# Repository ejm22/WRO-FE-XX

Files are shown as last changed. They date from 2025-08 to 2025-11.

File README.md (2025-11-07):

# WRO-FE-XX
Documentation for team Double-X's robot for WRO 2025 - Future Engineers.

If you're searching for the National Final version of the code, you can find the file main.py (National Final version) in the same file as run.py (International Final version). Both codes work if you'd like to try Version 1.

---

## Summary Video
This 6 minutes video summarizes our project and documentation. We recommend you watch it to easily and efficiently understand our project !

Summmary Video (https://www.youtube.com/watch?v=--gac5zhfu8 "Summary Video")

## The Team
Team Double-X is made of 2 engineering students, Michael Bruneau and Emile Jacques, and we've been teammates since 2015 !  
[Our Facebook Page since 2015](https://www.facebook.com/1WROCanadaDoubleX)

<table>
  <tr>
    <td>Michael Bruneau</td>
    <td>Emile Jacques</td>
  </tr>
  <tr>
    <td>Michael Bruneau</td>
    <td>Michael Bruneau</td>
  </tr>
</table>

---

## The Robot (Slef)
Have you ever had methods in your class needing the 'self' input to access the object ? If so, we are absolutely sure you've at least misstyped it once. Which is what we did throughout the entire project. With the amount of times Emile typed 'Slef', we had to give this name to our robot haha.

### Pictures

<table>
  <tr>
    <td align="center"><strong>GIF</strong><br></td>
  </tr>
</table>

---

<table>
  <tr>
    <td align="center"><strong>Top</strong><br></td>
    <td align="center"><strong>Front</strong><br></td>
    <td align="center"><strong>Left</strong><br></td>
  </tr>
  <tr>
    <td align="center"><strong>Bottom</strong><br></td>
    <td align="center"><strong>Back</strong><br></td>
    <td align="center"><strong>Right</strong><br></td>
  </tr>
</table>

#### Recent Modifications
A few hardware modifications were brought since these pictures were taken. 
- **Stepper Motor & Driver Wiring:** The wiring was simplified to remove one terminal block and multiple solid wires.
- **White Tape Replaced:** The white tape that used to be on top of the servo motor was replaced by a thin 3D-printed white plate.
- **Canadian Flags:** A few Canadian flags were added to personalized our robot, since we are proud to represent Canada once again !

---

## Performance Videos
### Challenge 1
[Open Challenge Video for International Final on Youtube: ](https://youtu.be/sGerwb-1xKw)

[Open Challenge Video for National Final on Youtube: ](https://youtu.be/OgR29EYXkdw)

### Challenge 2
[Obstacle Challenge Video for International Final on Youtube: ](https://youtu.be/1s1PPFf92Jc)

[Obstacle Challenge Video for National Final on Youtube: ](https://youtu.be/s9inOFHvLYA)

---

## Mobility Management

- **Dimensions:** width 135mm, length 285mm for tight turns and component fit, height 248mm.  
  [Why we chose those dimensions](mech/README_mech.md#14-dimensions-choice)
- **Drive Motor:** NEMA 17 stepper (precise, no encoder needed).
We calculated the needed torque for our application, and considering a rolling resistance and an 85% gearbox efficiency, the NEMA-17's torque is greater than the needed torque. Here's how we calculated it : 


  [More Information on Drive Motor Choice](elec/README_elec.md#13-motor-choice)
- **Steering Motor:** Standard servo motor for simple, precise steering.  
  [More Information on Steering Motor Choice](elec/README_elec.md#14-direction-control--servo-motor)
- **3D-Printed Structure:** Three-layer design (base, middle, top) for easy assembly and access.  










  [More Pictures & Info Here](mech/README_mech.md#3-final-3d-printed-structure)
- **Custom Mounts:** Holders for servo, stepper, switches, camera, and stepper coupler.  
  [Pictures Here](mech/README_mech.md#4-mounting-and-coupling)
- **Steering:** Initially parallel beams, now Ackermann geometry, 3D-printed after Lego prototyping. 




  [Steering CADs](mech/README_mech.md#12-steering-system)
- **Wheels:** Spike Prime wheels (56mm diameter, 14mm thick) for compactness and grip.  
  [Why We Chose Spike Prime Wheels](mech/README_mech.md#11-wheel-choice)
- **Differential:** Compact differential for rear wheels, made of Lego pieces individually bought on BrickLink.  
  [Why We Chose This Differential](mech/README_mech.md#13-differential-rear-wheels)

- **Iterations:** As you can see in the following image, this was an iterative project with many versions of each part. 


#### Here's a general view of the robot in SolidWorks. The second picture is an exploded view of it, so you can see the detachable pieces.
<table>
  <tr>
    <td>Michael Bruneau</td>
    <td>Emile Jacques</td>
  </tr>
</table>

### Controlling the Motors
This following document explains the C++ code used by the Arduino to control both the stepper and servo motors.  
[Motor Control](code/md/motor_control.md)

---

## Building Instructions
- **Parts list**\
Make sure you have all components ready before starting: 3D-printed parts, motors, drivers, electronics, screws, and connectors. A complete detailed table with quantities, sources, and usage is included below for reference.\
[Click here to open the parts list](XX_Parts_Lists.pdf)
- **3D Printing Parts**\
Using any 3D printer, start by 3D printing the necessary parts for the assembly. We used a Prusa Core 1. Every part needed has a STL file which you can use with any printer. If you're adventurous and want to modify a part, open the STEP file in your favorite CAD software. If you're unsure of what part you're printing, make sure to open the PNG file which contains a picture of the part.\
[Click here to open this folder](mech/CAD_3D_Printed_Pieces)
- **Adjust the Driver**\
The DRV8825 has a tiny screw to adjust the maximum current output. This isn't a big problem since the NEMA 17 stepper motor requires barely a few hundred mA, but it's good practice to set a limit. Use the DRV8825 Adjuster we custom-built to set this limit ! You can recreate this adjuster using the following drawing.\
[DRV8825 Adjuster Drawing](elec/Driver_Calibration_Circuit.pdf)
<table>
  <tr>
    <td>Michael Bruneau</td>
    <td>Emile Jacques</td>
  </tr>
</table>

- **Assemble the Robot**\
Mechanically assembling the robot is quite straight-forward. The tricky part comes with the electrical connections. Make sure you follow correctly the following electrical drawings.\
*Take notes, the drawings are quite small ! Make sure to download the PDF files to be able to zoom.*\
[Electrical Drawings](elec/Electric_Planning.pdf)

---

## Power & Sense Management

### Hardware Architecture
The "brain" of our robot is a Raspberry Pi 5, coded in Python. Connected to it is the Pi Camera 3 wide angle, meaning that all data will be directly given to the Pi. The Pi is also connected to an Arduino Uno R3, coded in C++, which controls the servo motor and the stepper motor's driver. The Arduino receives its commands via serial communication from the Pi. The stepper motor's driver will then power the motor if needed. 

<table>
  <tr>
    <td>Michael Bruneau</td>
  </tr>
</table>

- **Controller:** Raspberry Pi 5 (vision+logic, master) + Arduino Uno R3 (motor driver, slave).  
  [Why We Chose the Pi 5](elec/README_elec.md#21-main-components-choice)
- **Stepper Driver:** DRV8825 on breadboard (micro-stepping).  
  [Why We Chose the DRV8825](elec/README_elec.md#21-main-components-choice)
- **Camera:** Pi Camera 3 Wide for large FOV—helps with vision and parking.  
  [Why We Chose the Pi Camera 3 Wide](elec/README_elec.md#21-main-components-choice)
- **Wiring:** Terminal blocks and breadboard help organize and distribute power/signals.  
  [More details](elec/README_elec.md#3-wiring-and-distribution)
- **Power:** 4s1p 18650 Li-ion (14.4V) pack, DC/DC converter to 5V, terminal blocks for safe distribution.  

### Battery Runtime Calculation (1 hour at max load)
Here is the table of component power requirements : 

| Component | Voltage Requirement | Current Requirement |
|---|:---:|:---:|
| **Raspberry Pi 5** | 5V | up to 3A |
| **Arduino Uno R3** | 5V | ~40mA |
| **NEMA 17 Stepper Motor**  | 12V (via driver) | Via Driver (so 0)  |
| **DRV8825 Stepper Driver** | 12V | ~700mA |
| **Servo Motor (steering)** | 5V | ~700mA |
| **Pi Camera 3 Wide** | 5V (via Pi) | Via Pi (so 0) |
| **DC/DC Converter** | 14.4V in, 5V out | 80% efficiency |
| **4s1p 18650 Li-Ion Pack** | 14.4V | up to 2.85A |

Given the table, here's a quick calculation for **1 hour** of operation at maximum power:

#### Step 1: 5V Side Consumption
- Raspberry Pi 5: 3.00A  
- Arduino Uno R3: 0.04A  
- Servo Motor: 0.70A  
- **Total 5V current:** 3.74A  

**Power at 5V:**  
3.74A × 5V = **18.7W**

#### Step 2: Account for DC/DC Efficiency (80%)
**Battery power needed for 5V rail:**  
18.7W / 0.8 = **23.4W**

#### Step 3: Add Stepper Driver (12V side)
DRV8825: 0.70A × 12V = **8.4W**

#### Step 4: Total Battery Power & Current
**Total power from battery:**  
23.4W (5V rail) + 8.4W (stepper) = **31.8W**  
**Current from battery:**  
31.8W / 12V = **2.65A**

#### Step 5: Battery Capacity Needed (1 hour)
2.65A × 1h = **2.65Ah**

#### Conclusion
At full load, 1 hour of runtime requires **2.65Ah** at 12V.  
The 4s1p 18650 pack (2.85Ah) is just enough for 1 hour at max draw.

**In practice:** Most components use less than max (the Pi uses less than half), the robot is often idle, the DC/DC's efficiency is actually closer to 86%, and the stepper driver is disabled at 0 speed. In real use, the robot lasts 3–4 times longer, so the 4s1p pack is more than sufficient. We also have 8 cells in total so while 4 of them are used, the other 4 are charging, and it takes less time to charge batteries to full than to empty them.

### Security Measures
We added many security mesures on our robot to assure a safe robot and minimal reliability issues with parts.
- **Fuse:** We use a 3A fuse between the battery pack and the rest of the robot's electrical connexions to ensure the pack's safety.
- **Switches:** A Main Switch and a Driver Switch are installed. We are then able to shutdown the stepper motor in one click, or the entire robot in one different click.
- **Front Wing (Bumper):** A front wing was added to the front of the robot to make it crashproof. This keeps the important mechanical and electrical parts of the robot from absorbing the shock.
- **Terminal Blocks:** Terminal blocks were added for safer and easier electrical connexions. No short circuits in sight :)
- **Battery Pack Orientation:** Some of the cells would sometimes move too much from an impact between the robot and the wall, even with the bumper. By rotating the pack by 90 degrees, the cells won't be able to move.
- **Voltmeter:** A voltmeter was added on the side of the robot, connected right after the fuse, to show the battery pack's voltage. This is extremely useful since we preferably never want our voltage to go below 10.8V (for cell preservation). 

---

## Obstacle Management

### Vision Methods and Decision Making

This part of the readme explains how the computer vision pipeline drives steering decisions for the robot. It explains the following:
- Wall following (how far up the image it sees black on both sides)
- Obstacle handling
- Inner/outer crash detection
- Arbitration (how actions are chosen)

### 1) Image pipeline (inputs used by algorithms)

The camera pipeline produces these images used by the algorithms:
- polygon_image: binary map of the drivable corridor (walls are black=0, free space is white=255)
- display_image: BGR frame used for debug overlays (text, lines, circles)
- obstacle_image / pink_obstacle_image: binary masks for color obstacles
- blueline_image & orangeline_image: per-color masks for lap tracking

<table>
  <tr>
    <td align="center">
      <strong>Display Image Open Challenge</strong><br>
      
    </td>
  </tr>
  <tr>
    <td align="center">
      <strong>Display Image Obstacle Challenge</strong><br>
      
    </td>
  </tr>
  <p>*The display image contains new information such as the state of the program, a timer and the speed.</p>
  <tr>
    <td align="center">
      <strong>Polygon Image</strong><br>
      
    </td>
  </tr>
  <tr>
    <td align="center">
      <strong>Obstacle Image</strong><br>
      
    </td>
  </tr>
  <tr>
    <td align="center">
      <strong>Lines Image</strong><br>
      
    </td>
  </tr>
</table>

See [`CameraManager`](code/XX_2025_package/classes/camera_manager.py) and [`ImageTransformUtils`](code/XX_2025_package/utils/image_transform_utils.py).

### 2) Wall following calculations

Goal: steer so that the nearest wall is observed at a desired “depth” (how far up the image) and “lateral” position (how far from the side).

How it works:
- The robot scans for black (wall) pixels:
  - Bottom-up along a small band of columns near the followed side (“how far up” the wall appears).
  - Side-in from the image center toward the followed side along a small band of rows (“how far inward” the wall appears).
- These samples are averaged into (avg_x, avg_y) by [`ImageAlgorithms.find_wall_to_follow`](code/XX_2025_package/classes/image_algoriths.py).
- [`ImageAlgorithms.calculate_servo_angle_from_walls`](code/XX_2025_package/classes/image_algoriths.py) builds a PD-like controller:
  - Proportional term: error = (avg_x + avg_y) − threshold.
  - Derivative term: change of that error across frames.
  - Direction sign (LEFT/RIGHT) is taken from context to steer the correct side.
- Gains and the target threshold come from [`CHALLENGE_CONFIG`](code/XX_2025_package/classes/image_algoriths.py) via [`ImageAlgorithms.calculate_wall_threshold_kp_kd`](code/XX_2025_package/classes/image_algoriths.py), adapting behavior per challenge/lap.
- Corner detection: a large negative jump in the wall error derivative marks a “corner,” returned via the is_corner flag for higher-level logic.

Notes:
- “How far up it sees black on both sides” is embodied in the dual scans (bottom-up and side-in) that together capture corridor geometry.

### 3) Obstacle handling calculations

When an obstacle is present (green/red/pink block), the robot computes an avoidance “object line,” converts it to an angle, and arbitrates with wall following. The robot will accelerate between obstacles.

Process in [`ImageAlgorithms.find_obstacle_angle_and_draw_lines`](code/XX_2025_package/classes/image_algoriths.py):
- Safety first: [`ImageAlgorithms.check_outer_wall_crash`](code/XX_2025_package/classes/image_algoriths.py) and [`ImageAlgorithms.check_inner_wall_crash`](code/XX_2025_package/classes/image_algoriths.py). If a frontal collision risk is detected, immediately force a sharp evasive turn.
- Find the largest / lowest obstacle rectangle on the color mask image and classify its color using HSV.
- Draw a guidance line from the obstacle center to a safe floor target x:
  - Green → pass on the right; Red → pass on the left (policy).
- Convert that line’s geometry into an object angle, then map it to a servo angle with a color-specific offset in [`ImageAlgorithms.calculate_servo_angle_from_obstacle`](code/XX_2025_package/classes/image_algoriths.py).
- Inner safety: [`ImageAlgorithms.check_inner_wall_crash`](code/XX_2025_package/classes/image_algoriths.py) disables obstacle passing if the inner wall is too close (falls back to wall following).

What the “mapping” does:
- It shifts and scales the object angle around straight-ahead so the servo turns just enough to skirt the obstacle, clamped to safe servo limits.

### 4) Crash detection

Two safety checks override normal behavior:
- Outer wall crash: [`ImageAlgorithms.check_outer_wall_crash`](code/XX_2025_package/classes/image_algoriths.py) probes a fixed point ahead, and if it’s black in the polygon image, commands an emergency turn away from the outer wall.
- Inner wall crash: [`ImageAlgorithms.check_inner_wall_crash`](code/XX_2025_package/classes/image_algoriths.py) probes several points near the inner side; if too close (especially with a short obstacle), obstacle passing is suppressed.

### 5) Arbitration: choosing the action

Both proposals are produced:
- Wall-following angle from [`ImageAlgorithms.calculate_servo_angle_from_walls`](code/XX_2025_package/classes/image_algoriths.py)
- Obstacle angle from [`ImageAlgorithms.calculate_servo_angle_from_obstacle`](code/XX_2025_package/classes/image_algoriths.py) (or None if no obstacle)

Selection rule in [`ImageAlgorithms.choose_output_angle`](code/XX_2025_package/classes/image_algoriths.py):
- If there is a valid obstacle-avoidance angle, prefer it; otherwise, follow the wall.

Priority in practice:
1) Outer wall crash → emergency avoidance
2) Valid obstacle avoidance → use it
3) Inner wall too close while avoiding → fall back to wall following
4) Otherwise → wall following

### 6) Tuning notes

- Controller gains/thresholds are challenge-aware via [`CHALLENGE_CONFIG`](code/XX_2025_package/classes/image_algoriths.py) and refined per lap in [`ImageAlgorithms.calculate_wall_threshold_kp_kd`](code/XX_2025_package/classes/image_algoriths.py).
- The direction (LEFT/RIGHT) simply flips the sign of the control so one algorithm works for both sides.
- Corner detection from the wall controller’s derivative is used elsewhere (for example during parking) to trigger special maneuvers.

───────────────

### Block diagrams:
<table>
  <tr>
    <td align="center">
      <strong>Open Challenge Block Diagram</strong><br>
      
    </td>
  </tr>
  <tr>
    <td align="center">
      <strong>Obstacle Challenge Block Diagram</strong><br>
      
    </td>
  </tr>
  <tr>
    <td align="center">
      <strong>Obstacle Challenge Action Decisions</strong><br>
      
    </td>
  </tr>
</table>

### Extras
- Lap tracking and direction detection [details here.](code/md/laps_and_direction.md)
- Parking [details here.](code/md/parking.md)

---

## Software Key Components

- **Communication:** Serial communication via USB cable between Arduino and Pi (using custom protocol).\
  [Communications Protocol Details](code/md/communication.md)
- **Raspberry Pi Environment Setup:** Downloading utilities on your Pi, creating a virtual environment (venv), and installing dependencies.\
  [How to Setup your Raspberry Pi](code/md/raspberry_pi_setup.md)

---

## Possible Improvements
- **Holding the Raspberry Pi Better:**
The Raspberry Pi is currently fixed with black electric tape. Ideally, a simple detachable 3D-printed part could hold it.
- **Cutting Power Automatically at 10.8V:**
Whenever the battery pack voltage is below 10.8V, we would open the circuit to ensure that the circuit shuts down.
- **Replacing the Breadboard with Custom PCB:**
Instead of using a breadboard with mediocre cable management, we would simply add a custom PCB where we would solder the necessary cables in place.
- **Adding Lateral Distance Sensors:**
The current one-camera solution is complex to work with for the parallel parking. We would add distance sensors on both sides to detect the parking parking when we pass by, and to improve the overall wall detections across both challenges.
- **Adding Dynamic Ranges for Colors:**
The HSV ranges we have are set for the entire run. If we had more time, we would love to add dynamic ranges to account for walls / obstacles that appear lighter because of lighting on certain part of the wall, because of windows for example.

---

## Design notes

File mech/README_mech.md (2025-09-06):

### Mechanical Design Approach
[All PNG, STP and STL files are in this directory](./CAD_3D_Printed_Pieces/)
#### 1\. Basic Mechanical Choices

###### **1.1 Wheel Choice**
We chose Spike Prime wheels (56mm diameter, 14mm thickness) for their compactness, grip on vinyl, and familiarity. Larger wheels would make the robot harder to control and take too much space; smaller wheels would complicate the design and lower ground clearance.


###### **1.2 Steering System** 
- **Prototype:** Parallel beam Lego steering (two beams linked at ends) was tested. It suffered from drifting during turns due to both wheels turning at the same radius.

- **Ackermann Steering:** Lego-based Ackermann system was built to solve drifting. Final version is 3D-printed to fit the custom base plate.


###### **1.3 Differential (Rear Wheels)** 
A differential built out of Lego pieces individually bought on BrickLink allows the rear wheels to turn at different speeds for smooth cornering. Printing our own gears would have a low value/complexity ratio, so we built it with Lego pieces. It is very compact and works perfectly fine.
###### **1.4 Dimensions Choice**
We linked both the direction and differential wheel systems together. Considering all the components we would need to fit (Pi, Arduino, stepper motor, ...), we decided to keep a minimum approximate 50mm margin for the width, so max 150mm. A robot that has a big length/width ratio has a big turning radius (like a Formula 1 car). After testing different sizes, we decided to make the robot about 285mm long and 135mm wide. This makes the turning radius small enough to leave barely any room while turning around a pillar. 

---

#### 2\. Structural Prototypes

- **Lego Prototype:** Used 15-hole beams, L-beams, and frames to connect steering and differential systems.
- **Motor Positioning:** Stepper motor centrally located, axle connected to differential.
- **Wheel Space:** Front kept thin for steering range.
- **First Layer:** Held drive motor, DC/DC converter, and servo.


---

#### 3\. Final 3D-Printed Structure

- **Base Plate:** Holds wheel systems, stepper, DC/DC, and servo.
<table>
  <tr>
    <td align="center">
      <strong>BasePlaqueV4 CAD</strong><br>
      
    </td>
  </tr>
  <tr>
    <td align="center">
      <strong>BasePlaqueV4 Installation</strong><br>
      
    </td>
  </tr>
</table>

___

- **Middle Plate:** Holds battery pack, Arduino, terminal blocks, stepper driver (on breadboard), and switches.
<table>
  <tr>
    <td align="center">
      <strong>MiddlePlaqueV4 CAD</strong><br>
      
    </td>
  </tr>
  <tr>
    <td align="center">
      <strong>MiddlePlaqueV4 Installation</strong><br>
      
    </td>
  </tr>
</table>

___

- **Top Plate:** Holds Raspberry Pi 5, Pi Camera, and driver terminal block.

<table>
  <tr>
    <td align="center">
      <strong>TopPlaqueV4 CAD</strong><br>
      
    </td>
  </tr>
</table>

___

- **3D Views of Complete Product**

<table>
  <tr>
    <td align="center">
      <strong>Left Side View</strong><br>
      
    </td>
  </tr>
  <tr>
    <td align="center">
      <strong>Top View</strong><br>
      
    </td>
  </tr>
  <tr>
    <td align="center">
      <strong>Bottom View</strong><br>
      
    </td>
  </tr>
</table>

---

#### 4\. Mounting and Coupling

- Custom holders for servo, stepper, switches, and camera.


___

- Stepper coupler connects motor to the differential.


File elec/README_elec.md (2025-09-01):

### Electrical Design Approach

#### 1\. Motorization

###### **1.1 Motor Option 1 : DC Motor**
DC motors are simple to control (on/off), useful for continuous forward movement, but require an encoder to determine position for precise tasks.
###### **1.2 Motor Option 2 : Stepper Motor**
Stepper motors move in discrete steps by activating electromagnets sequentially. They are ideal for short, precise movements and allow accurate position control without an encoder.
###### **1.3 Motor Choice**
We chose the stepper motor because it eliminates the need for an encoder, offers very precise position control (especially for parking), and is a new challenge to explore. The only complexity added is in task scheduling in software, which is manageable.
We also already had a NEMA 17 stepper motor, light and low consuming, which perfectly fitted on the base.
###### **1.4 Direction Control : Servo Motor**
A servo motor was selected for steering because it does not require a separate driver, has only three wires, and provides precise control.

---

#### 2\. Electric/Electronic Architecture

###### **2.1 Main Components Choice**
- **Processing:**  
  The robot uses a Raspberry Pi 5 as the master computer, handling camera input and all high-level decision logic. The Pi needs 5V at up to 3A.
- **Motor Control:**  
  An Arduino Uno R3 acts as the slave controller, receiving commands from the Pi and driving the motors. The Arduino requires 5V at 40mA (negligible).
- **Power:**  
  The stepper driver needs 12V. We use a 4s1p pack of 3.6V 18650 Li-Ion cells (14.4V, 2.85A). 14.4V is distributed via terminal blocks, then stepped down to 5V with a DC/DC converter for the Pi and Arduino.
- **Stepper Driver:**  
  The DRV8825 was chosen for its small size and micro-stepping ability (necessary for precise stepper control). Placed on a breadboard for easy connections.
- **Camera:**
  The Pi Camera 3 Wide module was chosen over the Pi Camera 3 module to have a wider field of view (FOV), necessary for more precision when parking, and helpful throughout the rest of the challenge as well.

---

#### 3. Wiring and Distribution
- **Terminal blocks** provide safe, compact power distribution for 14.4V and 5V rails.
- **Breadboard** is used for convenient connection of the stepper driver,  toggle switches, servo motor and other small electrical connections.

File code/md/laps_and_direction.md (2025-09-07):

# Direction Determination (Challenge 1 and 2) and Lap Tracking

This section explains:
- How the robot picks its driving direction at the start of Challenge 1 and Challenge 2
- How laps are tracked using a simple, debounced state machine

## Challenge 1: Direction from Blue vs Orange Line Length

At the start of Challenge 1, the robot decides whether to follow the left or right wall by comparing the detected lengths of the blue and orange lines. The decision is made in [`ImageAlgorithms.get_direction_from_lines`](code/XX_2025_package/classes/image_algoriths.py):
- If the blue line is longer than the orange line → follow LEFT
- Otherwise → follow RIGHT

Internally it reads per-frame measurements prepared by the camera pipeline (for example: `camera_manager.length_blue` and `camera_manager.length_orange`) and sets the direction in context.

Example (simplified):

```python
# Decide direction using line lengths (Challenge 1)
def get_direction_from_lines(self):
    # length_blue / length_orange are computed in the camera pipeline
    direction = Direction.LEFT if self.camera_manager.length_blue > self.camera_manager.length_orange else Direction.RIGHT
    self.context_manager.set_direction(direction)
```

Where it’s called in the main flow:
- See Challenge 1 setup in [code/XX_2025_package/main.py](code/XX_2025_package/main.py).

## Challenge 2: Direction from Free-Space (Left vs Right Half)

In Challenge 2, the robot decides the initial direction by comparing how much free space (white pixels) exists on the left half vs the right half of the drivable mask (`polygon_image`). This logic is in [`ImageAlgorithms.get_direction_from_parking`](code/XX_2025_package/classes/image_algoriths.py):
- Count white pixels in left half and right half of the binary polygon image
- If left has more white → LEFT, else → RIGHT

Example (simplified):

```python
# Decide direction from how open each half is (Challenge 2)
def get_direction_from_parking(self, camera_object):
    left_white = np.sum(camera_object.polygon_image[:, :ImageTransformUtils.PIC_WIDTH // 2] == 255)
    right_white = np.sum(camera_object.polygon_image[:, ImageTransformUtils.PIC_WIDTH // 2:] == 255)
    direction = Direction.LEFT if left_white > right_white else Direction.RIGHT
    self.context_manager.set_direction(direction)
```

Where it’s called in the main flow:
- See Challenge 2 setup in [code/XX_2025_package/main.py](code/XX_2025_package/main.py).

## Lap Tracking: Windowed Color Detection + State Machine

Laps are tracked by watching a small window near the center-bottom of the frame and advancing a state machine when the expected color appears. The sequence depends on the driving direction:
- Direction LEFT: expect BLUE then ORANGE
- Direction RIGHT: expect ORANGE then BLUE
- After detecting the pair, wait (debounce) before looking for the next pair

Window used for detection in [`LapTracker.process_image`](code/XX_2025_package/classes/lap_tracker.py):
- Rows: PIC_HEIGHT − 130 to PIC_HEIGHT − 30
- Columns: ±20 pixels around the center x

State machine (LEFT direction) in [`LapTracker._process_left_direction`](code/XX_2025_package/classes/lap_tracker.py):
- INITIAL_STATE → LOOKING_FOR_BLUE
- LOOKING_FOR_BLUE: if BLUE seen → LOOKING_FOR_ORANGE
- LOOKING_FOR_ORANGE: if ORANGE seen → increment quarter, go to WAITING_STATE
- WAITING_STATE: after ~0.5s debounce → LOOKING_FOR_BLUE

```python
def _process_left_direction(self, detected_color):
    # INITIAL → LOOKING_FOR_BLUE
    # WAITING → after 0.5s → LOOKING_FOR_BLUE
    # LOOKING_FOR_BLUE + BLUE → LOOKING_FOR_ORANGE
    # LOOKING_FOR_ORANGE + ORANGE → increment quarter → WAITING
    if self._state == LapState.INITIAL_STATE:
        self._state = LapState.LOOKING_FOR_BLUE

    if self._state == LapState.WAITING_STATE:
        if self.time_stamp == 0:
            self.time_stamp = time.time()
        if time.time() - self.time_stamp >= 0.5:
            self._state = LapState.LOOKING_FOR_BLUE
            self.time_stamp = time.time()

    elif self._state == LapState.LOOKING_FOR_BLUE and detected_color == Color.BLUE:
        self._state = LapState.LOOKING_FOR_ORANGE

    elif self._state == LapState.LOOKING_FOR_ORANGE and detected_color == Color.ORANGE:
        self.context_manager.increment_quarter_lap_count()
        self._state = LapState.WAITING_STATE
```

State machine (RIGHT direction) in [`LapTracker._process_right_direction`](code/XX_2025_package/classes/lap_tracker.py) mirrors the logic:
- INITIAL_STATE → LOOKING_FOR_ORANGE
- LOOKING_FOR_ORANGE: if ORANGE seen → LOOKING_FOR_BLUE
- LOOKING_FOR_BLUE: if BLUE seen → increment quarter, go to WAITING_STATE
- WAITING_STATE: after ~0.5s → LOOKING_FOR_ORANGE

Quarter and lap accounting:
- Every time the color pair completes, [`ContextManager.increment_quarter_lap_count`](code/XX_2025_package/classes/context_manager.py) is called.
- The context tracks quarter count and laps; when enough quarters have been seen, the lap count increases.
- [`ContextManager.is_last_quarter`](code/XX_2025_package/classes/context_manager.py) and [`ContextManager.has_completed_laps`](code/XX_2025_package/classes/context_manager.py) are used to slow down or stop after the goal.

Block diagram:
<td>lap_drawio</td>
<br><br>

## End-to-End Usage Snippet

In the main loop ([code/XX_2025_package/main.py](code/XX_2025_package/main.py)):

```python
# Challenge 1: direction from lines
image_algorithms.get_direction_from_lines()

# Challenge 2: direction from free-space split
image_algorithms.get_direction_from_parking(camera_manager)

# While driving: update lap tracking from the window
lap_tracker.process_image(camera_manager.cnt_blueline, camera_manager.cnt_orangeline)

# Example of reacting to final quarter
if context_manager.is_last_quarter():
    speed = 4000  # slow down on final approach
```

This approach gives a robust start-direction choice for both challenges and a simple, debounced lap tracker.

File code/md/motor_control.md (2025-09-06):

# How We Control the Motors

This document explains how the drive and steering motors of Team Double-X's robot are controlled using Arduino, focusing on our actual implementation and challenges.

---

## 1. Overview

Our robot uses:
- **NEMA 17 Stepper Motor** for driving the rear wheels (precise position & speed control).
- **Servo Motor** for steering the front wheels (Ackermann geometry).

The motors are controlled by an **Arduino Uno R3** that receives high-level commands from a Raspberry Pi 5 and drives the motors using dedicated libraries and electronic drivers.

---

## 2. Hardware Architecture

- **Stepper Motor Driver:** DRV8825, chosen for its microstepping ability and compact design.
- **Connections:**  
  - Stepper motor uses STEP, DIR, and ENABLE pins.
  - Servo motor uses a single PWM pin (ANGLE_PIN).
- **Power:**  
  - Stepper driver powered by 12V from a Li-Ion pack.
  - Arduino and Pi powered via a DC/DC converter.

---

## 3. Arduino Software Implementation

Our code for motor control is written in C++ and runs on the Arduino. The logic is split between stepper (drive) and servo (steering) control.

### Stepper Motor Control (Drive)

A stepper motor functions by receiving pulses which activate and deactivate magnets, turning the motor. When decelerating, a stepper can't keep its precision if it stops receiving steps, hence why we need to gradually lower the speed. We use the FlexyStepper library, because it can manage those decelerations. The command logic is our own. The driver is **enabled** only when movement is required; otherwise, it is disabled to prevent overheating.

```cpp
#include <FlexyStepper.h>

const int DIR_PIN = 10;
const int STEP_PIN = 9;
const int ENABLE_PIN = 2;

FlexyStepper stepper;

void setup() {
    stepper.connectToPins(STEP_PIN, DIR_PIN);
    pinMode(ENABLE_PIN, OUTPUT);
    digitalWrite(ENABLE_PIN, LOW); // Enable driver by default
}

void loop() {
    // Example: Move the robot if a command is received
    if (shouldMove()) {
        digitalWrite(ENABLE_PIN, LOW); // Enable driver
        stepper.setSpeedInStepsPerSecond(commandedSpeed);
        stepper.setAccelerationInStepsPerSecondPerSecond(2000);
        stepper.moveRelativeInSteps(commandedSteps);
    } else if (currentSpeedIsLowEnough()) {
        digitalWrite(ENABLE_PIN, HIGH); // Disable driver to avoid overheating
    }
}
```

### Servo Motor Control (Steering)

Steering is achieved with a standard Servo library. The servo receives new angles as commands are processed.

```cpp
#include <Servo.h>
const int ANGLE_PIN = 11;

Servo steeringServo;

void setup() {
    steeringServo.attach(ANGLE_PIN);
}

void loop() {
    int steeringAngle = getSteeringAngle();
    steeringServo.write(steeringAngle); // Angle: 36-136
}
```
*Note: The angle at which the servo is straight is 86 degrees. The maximum angles for our Ackermann steering are 36 and 136 degrees.*

---

## 4. Control Flow

1. **Command Reception:**  
   The Pi sends commands to the Arduino (distance, speed, steering angle).
2. **Motion Execution:**  
   - Arduino sets the stepper speed, servo angle, and target position.
   - Driver ENABLE is managed based on demand and speed.
3. **Safety & Scheduling:**  
   - The driver is disabled when no motion is needed, or the speed is near zero, to prevent overheating.
   - Motion complete functions ensure safe synchronization.

---

## 5. Temperature Analysis

A major issue we encountered is **driver overheating**. The DRV8825 gets extremely hot even with moderate use, especially if it's left enabled while idle. To address this, our code disables the driver whenever:
- The demanded speed is zero and the actual speed is low enough.
- No commands are received for a while.

Below are thermal images showing the results of our code:

<table>
  <tr>
    <td align="center">
      <strong>Stepper Driver and Servo Motor Temperatures</strong><br>
      
    </td>
  </tr>
  <tr>
    <td align="center">
      <strong>Robot Temperature Overview</strong><br>
      
    </td>
  </tr>
</table>

*Images show that the driver temperature is around 40 degrees Celsius, which is very normal. We do not have pictures, but it would previously be so hot that touching the driver could cause serious burns*

---

## 6. References

- [FlexyStepper Library Documentation](https://github.com/Stan-Reifel/FlexyStepper)
- [DRV8825 Datasheet](https://www.ti.com/lit/ds/symlink/drv8825.pdf?HQS=dis-dk-null-digikeymode-dsf-pf-null-wwe&ts=1752710261679)
- [Driver Circuit Used on our Robot: How to Adjust Current Limit](https://www.makerguides.com/drv8825-stepper-motor-driver-arduino-tutorial/)
- *Main Arduino code: [`code/arduino/src/main.cpp`](../code/arduino/src/main.cpp)*

---

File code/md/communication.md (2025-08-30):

# Communication Protocol

## Pi-Arduino Communication

The Raspberry Pi and Arduino communicate via USB serial connection. The Pi sends formatted commands to control the robot's movement, while the Arduino sends status updates back to the Pi.

### Communication Setup
- **Connection**: USB serial between Raspberry Pi and Arduino
- **Baud Rate**: 115200
- **Protocol**: Text-based commands with specific delimiters

### Command Format

#### Pi → Arduino (Movement Commands)
Commands for movement follow the format: `m{angle},{speed}.`
If there is a target distance: `t{angle},{speed},{target}`

| Command Format | Description | Example |
|---|---|---|
| `m{angle},{speed}.` | Move command with steering angle and motor speed | `m90,5500.` |
| `t{angle},{speed},{target}.` | Move command with angle, motor speed and target | `t90,5500,3000` |
| `10000000!` | Set target command (10000000 means never stop moving) | `10000000!` |

**Parameters:**
- `angle`: Servo angle for steering (typically 30-150, where 90 is straight)
- `speed`: Motor speed value (0-6000+ range)
- `target`: Motor rotation target in steps (0.1559 mm per 1 step) 
- `.` : Move command terminator
- `!` : New target command terminator

#### Arduino → Pi (Status Updates)
| Message | Description |
|---|---|
| `1` | Challenge 1 button pressed |
| `2` | Challenge 2 button pressed |
| `0` | Stop button pressed |
| `F` | Target reached after target movement command |

### Code Implementation

**Arduino Side** (`main.cpp`):
- Sends button press notifications to Pi
- Listens for serial commands
- Parses movement commands to extract angle and speed
- Controls servo and stepper motor accordingly
- Sends stop movement command after target reached

**Pi Side** (`main.py`):
- Listens for button press status from Arduino
- Handles challenge selection and stop commands
- Sends movement commands based on computer vision analysis

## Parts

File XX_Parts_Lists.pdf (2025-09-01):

Autonomous driving car Parts List WRO FE 2025
Team Double-X, Canada
Revision 2025-09-01
Item | P/N | Description | MFR | Source | Qty | Usage | Total Cost
1 | INR-18650-P30B | 3.7V 18650 cell | Molicel | 18650BatteryStore.com | 4 | Power pack | 28
2 | a15062200ux0651 | DPDT toggle switch | Uxcell | Amazon.ca | 2 | Power switches | 16
3 | 114090052 | Battery holder 18650 4 cells | Seeed Technology Co Digikey | 1 | Battery holder | 2
4 | 39367pb02 | Wheel 56 X 14 | Lego Group | Bricklink.com | 4 | Mechanical structure | 16
5 | KLF014 | Fuse holder | Kolacen | Digikey | 1 | Power | 1
6 | DC001 | 12V Male+Female 2.1x5.5MM DC Power Jack Plug Adapter Daykit | Amazon.ca | 1 | Power plugs | 2
7 | Generic | Radial Electrolytic Capacitor, 100uF, 16V | Generic | Amazon.ca | 1 | Stepper driver circuit | 0.5
8 | CER-795 | CERRXIAN 90 Degree USB A to B Cable | Lemeng | Amazon.ca | 1 | Pi to Arduino cable | 6.5
9 | SJ-15 | DRV8825 Stepper Motor Driver | SazkJere | Amazon.ca | 1 | Stepper driver | 5
10 | CA-EL-CP-006 | Mini Breadboard | Elegoo | Amazon.ca | 1 | Stepper driver circuit | 2
11 | X00413AO5J | Maixbomr Right Angle USB C to 2 Pin Bare Wire | Maixbomr | Amazon.ca | 1 | Pi power cable | 6
12 | 39100-1910 | Terminal blocks clear, 12 pos, 8 mm pitch | Molex | Mouser | 2 | Power connections | 5
13 | HS-225BB | Cored Nylon Gear 24T Analog Mini Servo | Hitec | Robotshop | 1 | Direction motor | 30
14 | RB-Ard-34 | Arduino Uno R3 USB Microcontroller | Arduino | Robotshop | 1 | Microcontroller | 28
15 | PI5-8GB-STR128-C4-BLK | Raspberry Pi 5 Starter Kit - Turbine Black | Raspberry Pi | Canakit | 1 | Main computer | 225
16 | PYBE30-Q24-S5-DIN | DC-DC converter 12V - 5V 6amps 30W | CUI | Digikey | 1 | Generate 5V from battery | 57
17 | B099JXQN6K | Polymaker PLA Filament 1.75 mm | Polymaker | Amazon.ca | 1 | Mechanical structure | 32
18 | BasePlaqueV4 | 3D printed base plate | Double-X | 3D printed | 1 | Mechanical structure | 0
19 | MiddlePlaqueV4 | 3D printed middle plate | Double-X | 3D printed | 1 | Mechanical structure | 0
20 | TopPlaqueV4 | 3D printed top plate | Double-X | 3D printed | 1 | Mechanical structure | 0
21 | CouplingV3 | 3D printed coupler | Double-X | 3D printed | 1 | Mechanical structure | 0
22 | ServoHolderV2 | 3D printed servo holder | Double-X | 3D printed | 1 | Mechanical structure | 0
23 | StepMotorBracket | 3D printed stepper holder | Double-X | 3D printed | 1 | Mechanical structure | 0
24 | FrontWingV2 | 3D printed bumper | Double-X | 3D printed | 1 | Mechanical structure | 0
25 | CamHolderV4 | 3D printed camera holder | Double-X | 3D printed | 1 | Mechanical structure | 0
26 | DirectionRods3 | 3D printed direction rod long | Double-X | 3D printed | 1 | Mechanical structure | 0
27 | DirectionRodsShort3 | 3D printed direction rod short | Double-X | 3D printed | 1 | Mechanical structure | 0
28 | DirectionTabs | 3D printed direction tabs (LH and RH) | Double-X | 3D printed | 1 | Mechanical structure | 0
29 | ButtonHolder | 3D printed switch holder | Double-X | 3D printed | 1 | Mechanical structure | 0
30 | 17HS4023 | Stepper motor NEMA 17 | Pancake Motor | Abra electronics | 1 | Drive motor | 27
31 | 527-1 | Raspberry Pi Camera module 3 wide + cable | Raspberry | Pishop | 1 | Camera | 49
32 | 3737 | Axle 10L | Lego Group | Bricklink.com | 2 | Rear axles | 0.5
33 | 87083 | Axle 4L with stop | Lego Group | Bricklink.com | 2 | Front axles | 0.5
34 | 3705 | Axle 4L | Lego Group | Bricklink.com | 1 | Stepper main axle | 0.25
35 | 3713 | Bushing | Lego Group | Bricklink.com | 8 | Mechanical structure | 0.5
36 | 4265 | half bushing | Lego Group | Bricklink.com | 4 | Mechanical structure | 0.25
37 | 6589 | Bevel gear 12 tooth | Lego Group | Bricklink.com | 3 | Mechanical structure | 0.25

38 | 62821b | Gear differential 28 tooth bevel | Lego Group | Bricklink.com | 1 | Mechanical structure | 1
39 | 64179 | Frame | Lego Group | Bricklink.com | 1 | Mechanical structure | 0.5
40 | JF-0039 | SPDT toggle switch | Jianfeng Store | Amazon.ca | 1 | Selector switch | 2
41 | PBS-110-XR | SPST push button momentary | Twidec | Amazon.ca | 1 | Start button | 1.7
42 | LS-1280 | M3 socket head screws, multiple length | HPGJLEE | Amazon.ca | 33 | Mechanical structure | 0.5
| | | | | | Total | 545.95

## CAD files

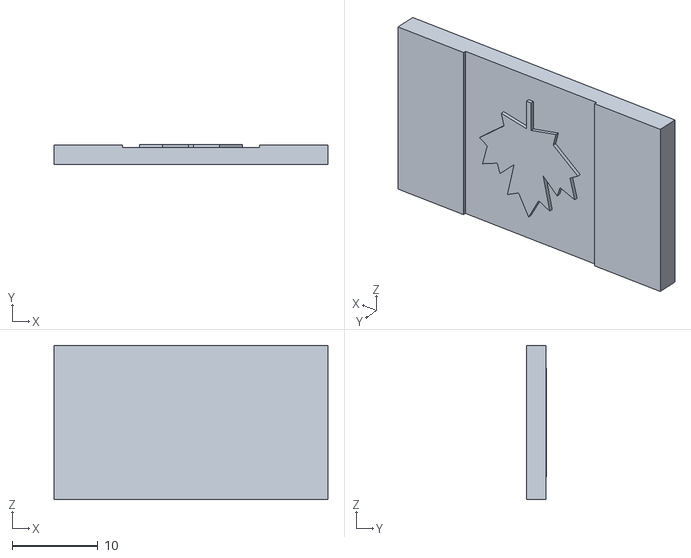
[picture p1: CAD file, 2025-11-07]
mech/CAD_3D_Printed_Pieces/CanadianFlag.STL
32.0 x 2.38 x 18.0

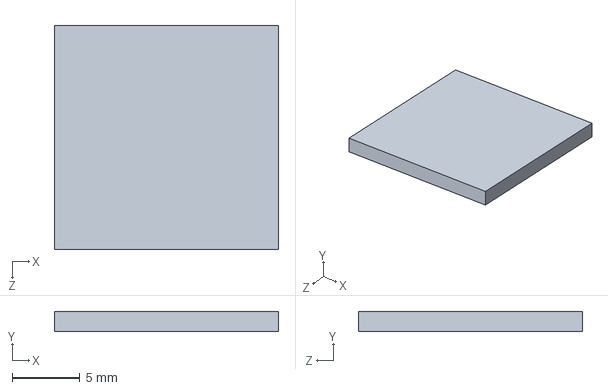
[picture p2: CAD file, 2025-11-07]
mech/CAD_3D_Printed_Pieces/ServoCover.SLDPRT
16.5 x 1.50 x 16.5 mm

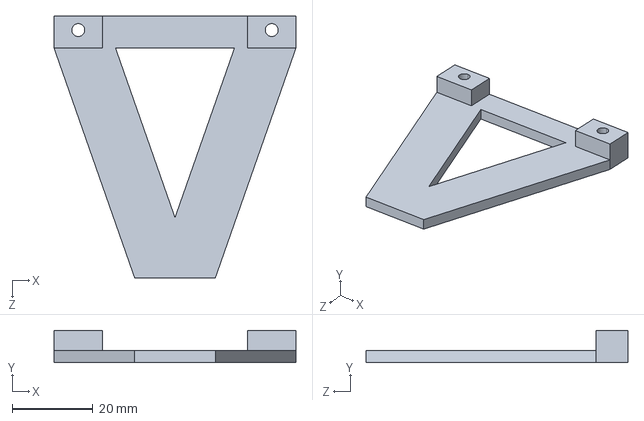
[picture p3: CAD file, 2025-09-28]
mech/CAD_3D_Printed_Pieces/FrontWingV2.STEP
60.0 x 8.00 x 65.0 mm

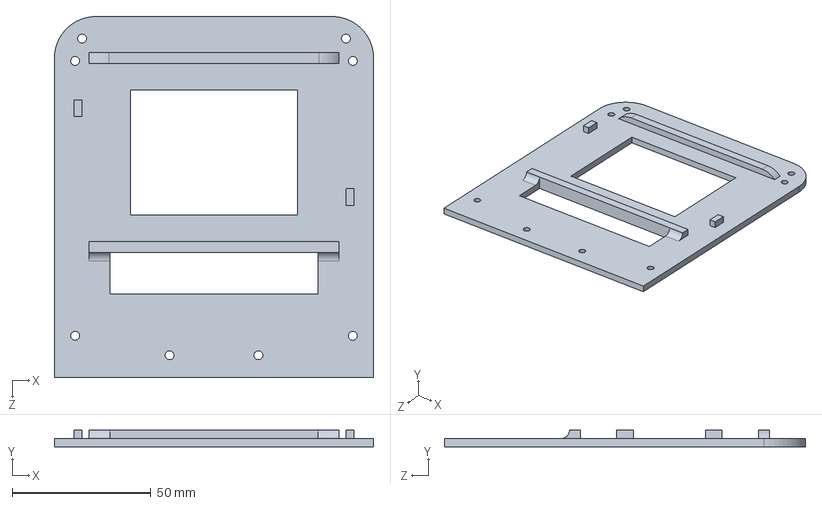
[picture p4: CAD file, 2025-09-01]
mech/CAD_3D_Printed_Pieces/TopPlaqueV4.STEP
115.0 x 6.00 x 130.0 mm

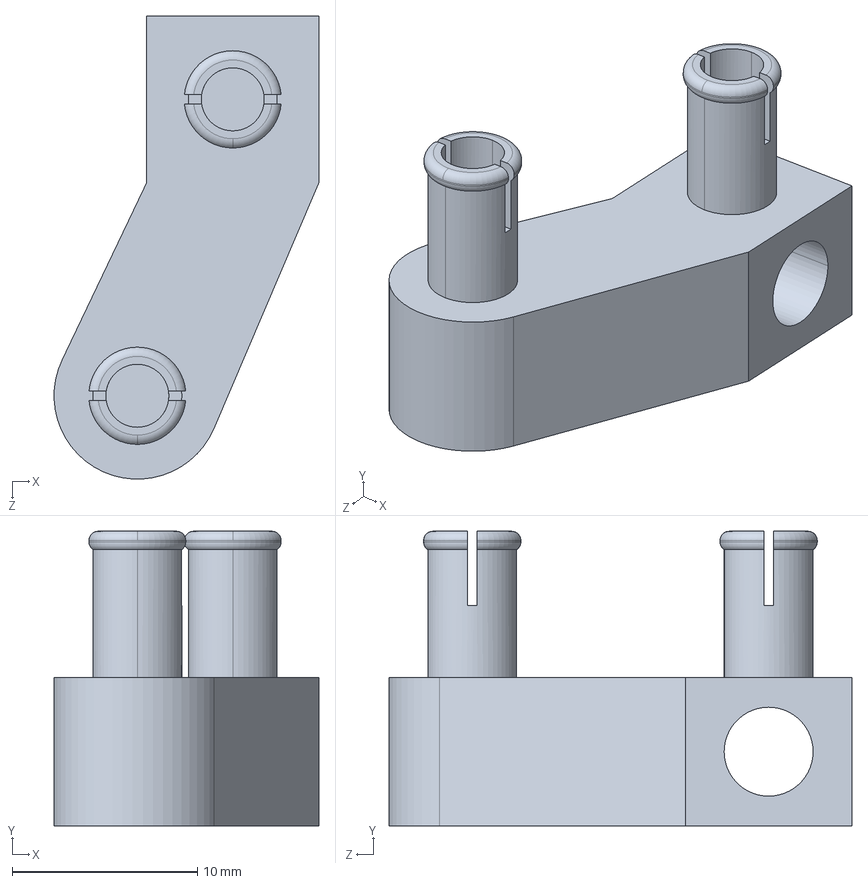
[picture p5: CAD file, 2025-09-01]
mech/CAD_3D_Printed_Pieces/DirectionTabsRH.STEP
14.3 x 15.9 x 25.0 mm

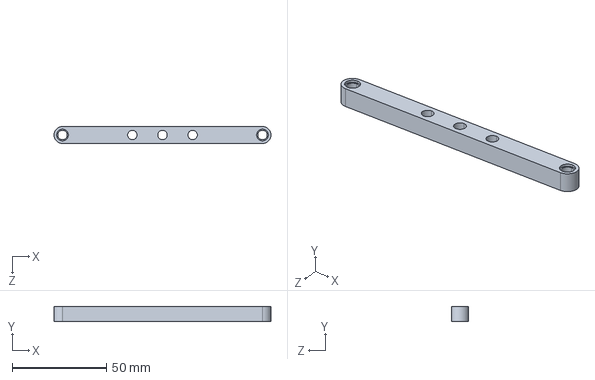
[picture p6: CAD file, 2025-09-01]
mech/CAD_3D_Printed_Pieces/DirectionRods3.STEP
115.3 x 8.00 x 9.00 mm

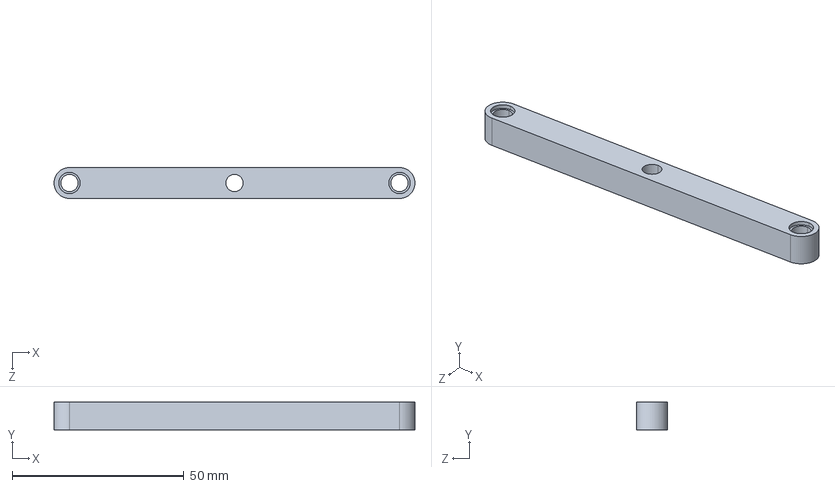
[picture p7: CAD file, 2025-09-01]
mech/CAD_3D_Printed_Pieces/DirectionRodsShort3.STEP
105.0 x 8.00 x 9.00 mm

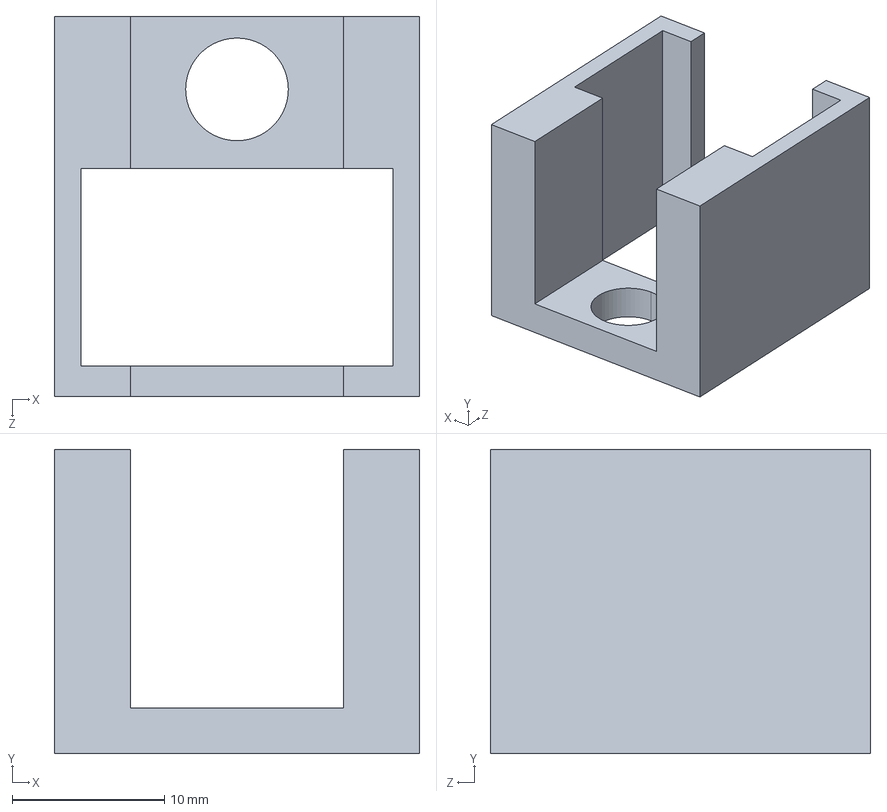
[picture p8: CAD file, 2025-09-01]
mech/CAD_3D_Printed_Pieces/ButtonHolder.STEP
24.0 x 20.0 x 25.0 mm

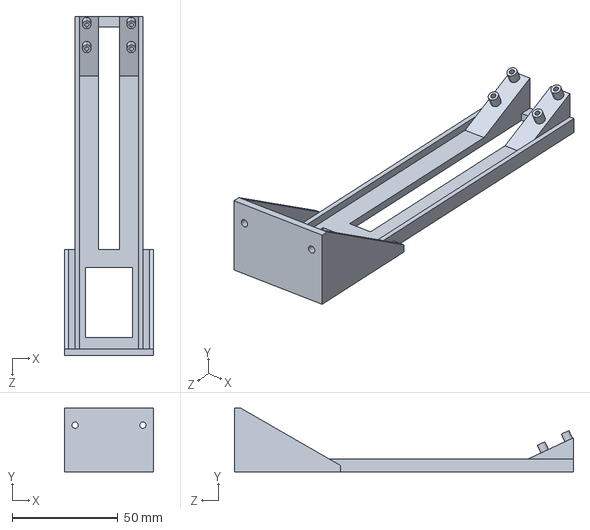
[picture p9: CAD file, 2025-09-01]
mech/CAD_3D_Printed_Pieces/CamHolderV4.STEP
42.0 x 30.0 x 160.0 mm

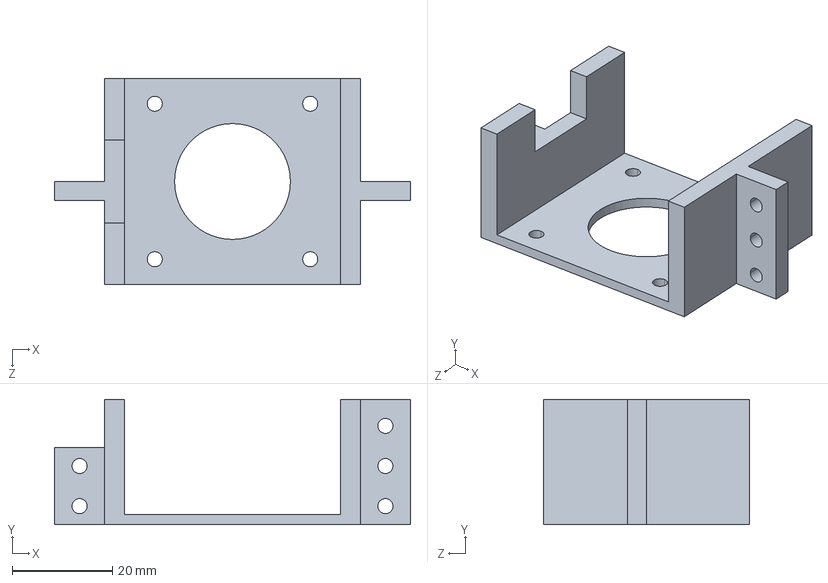
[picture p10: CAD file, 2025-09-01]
mech/CAD_3D_Printed_Pieces/StepMotorBracket.STEP
71.0 x 25.0 x 41.0 mm

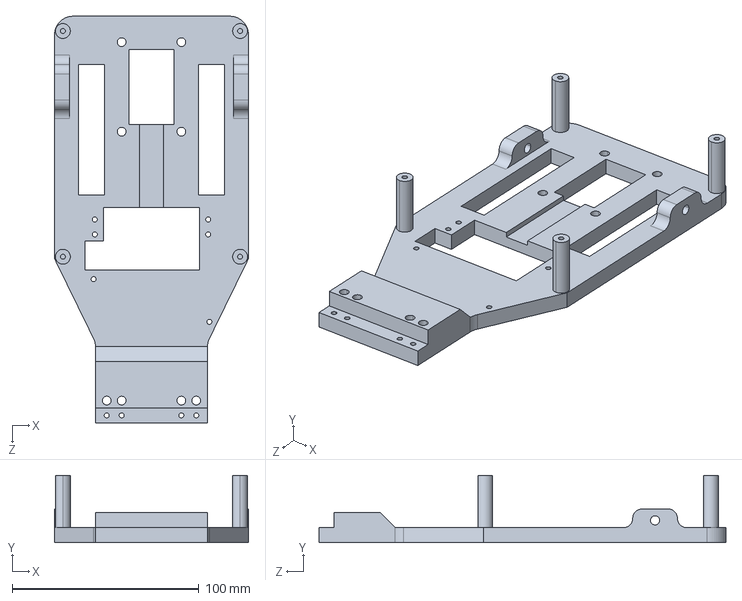
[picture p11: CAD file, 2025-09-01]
mech/CAD_3D_Printed_Pieces/BasePlaqueV4.STEP
104.0 x 36.0 x 218.0 mm

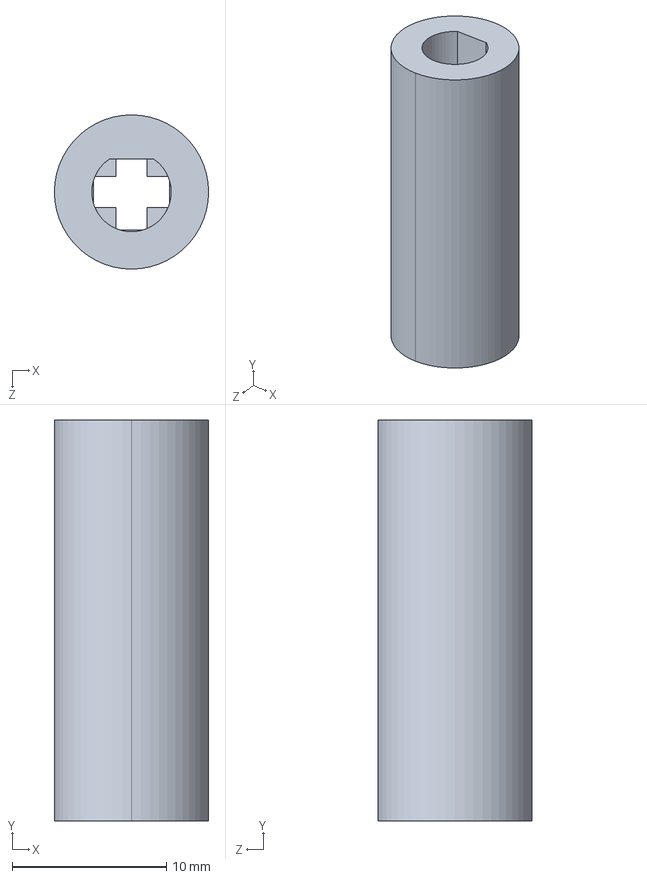
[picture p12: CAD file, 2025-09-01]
mech/CAD_3D_Printed_Pieces/CouplingV3.STEP
10.0 x 26.0 x 10.0 mm

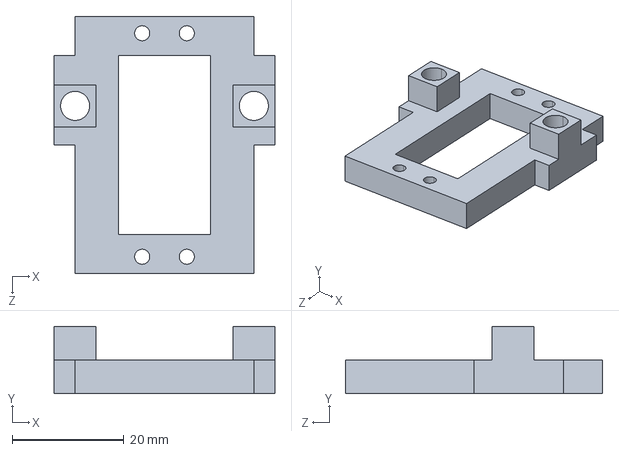
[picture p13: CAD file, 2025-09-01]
mech/CAD_3D_Printed_Pieces/ServoHolderV2.STEP
39.5 x 12.0 x 46.0 mm

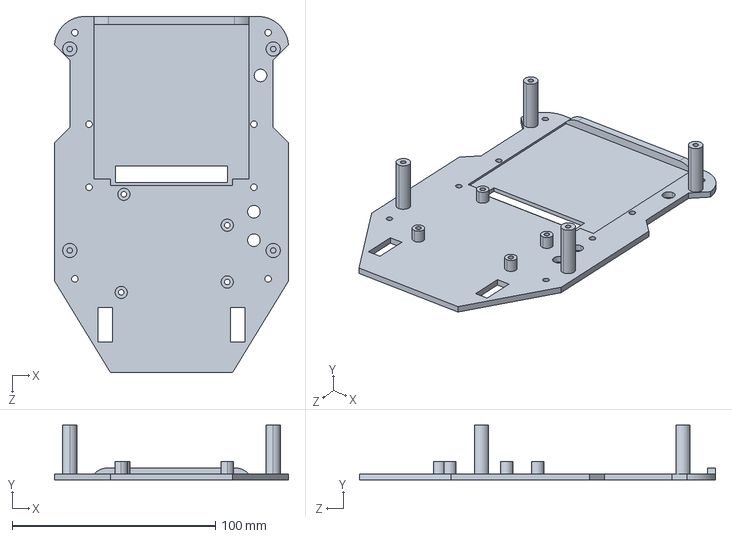
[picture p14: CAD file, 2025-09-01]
mech/CAD_3D_Printed_Pieces/MiddlePlaqueV4.STEP
115.0 x 27.0 x 175.0 mm

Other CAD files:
mech/CAD_3D_Printed_Pieces/DirectionTabsLH.STEP
mech/CAD_3D_Printed_Pieces/BasePlaqueV4.STL
mech/CAD_3D_Printed_Pieces/ButtonHolder.STL
mech/CAD_3D_Printed_Pieces/CamHolderV4.STL
mech/CAD_3D_Printed_Pieces/CouplingV3.STL
mech/CAD_3D_Printed_Pieces/DirectionRods3.STL
mech/CAD_3D_Printed_Pieces/DirectionRodsShort3.STL
mech/CAD_3D_Printed_Pieces/DirectionTabsLH.STL
mech/CAD_3D_Printed_Pieces/DirectionTabsRH.STL
mech/CAD_3D_Printed_Pieces/FrontWingV2.STL
mech/CAD_3D_Printed_Pieces/MiddlePlaqueV4.STL
mech/CAD_3D_Printed_Pieces/ServoCover.STL
mech/CAD_3D_Printed_Pieces/ServoHolderV2.STL
mech/CAD_3D_Printed_Pieces/StepMotorBracket.STL
mech/CAD_3D_Printed_Pieces/TopPlaqueV4.STL

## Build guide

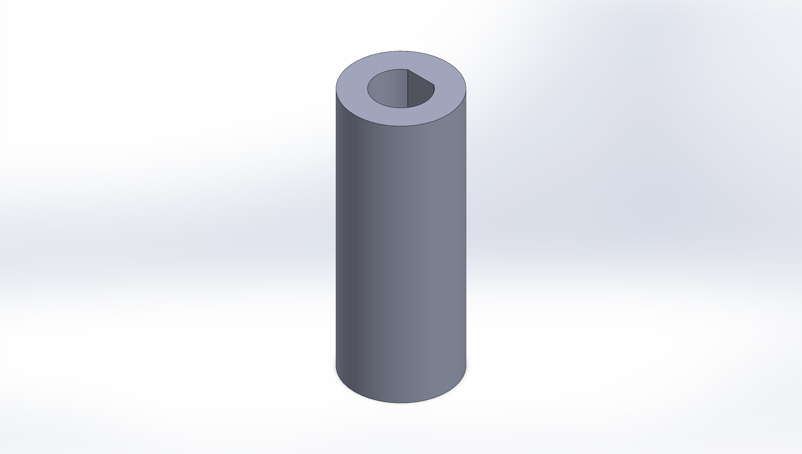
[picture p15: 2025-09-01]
v-photos/3D_Printed_PNG/CouplingV3.PNG

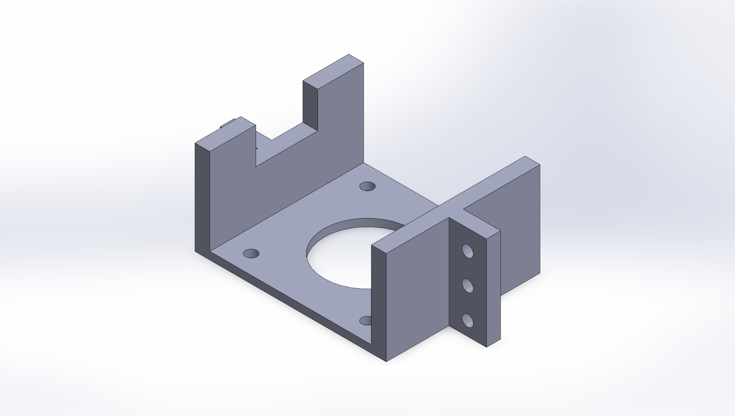
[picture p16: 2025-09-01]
v-photos/3D_Printed_PNG/StepMotorBracket.PNG

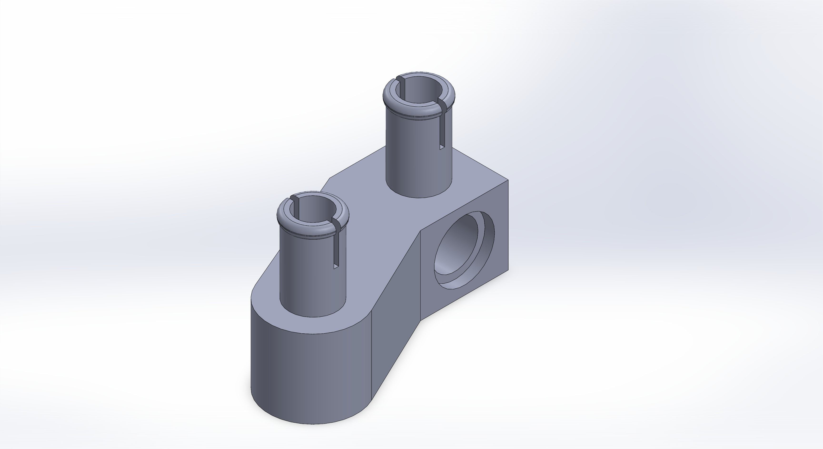
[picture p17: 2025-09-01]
v-photos/3D_Printed_PNG/DirectionTabsLH.PNG

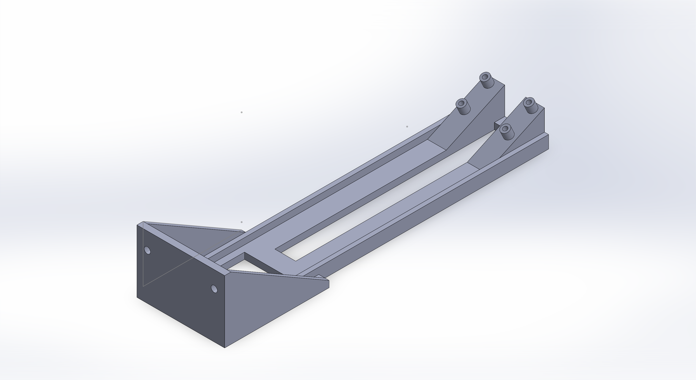
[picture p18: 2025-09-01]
v-photos/3D_Printed_PNG/CamHolderV4.PNG

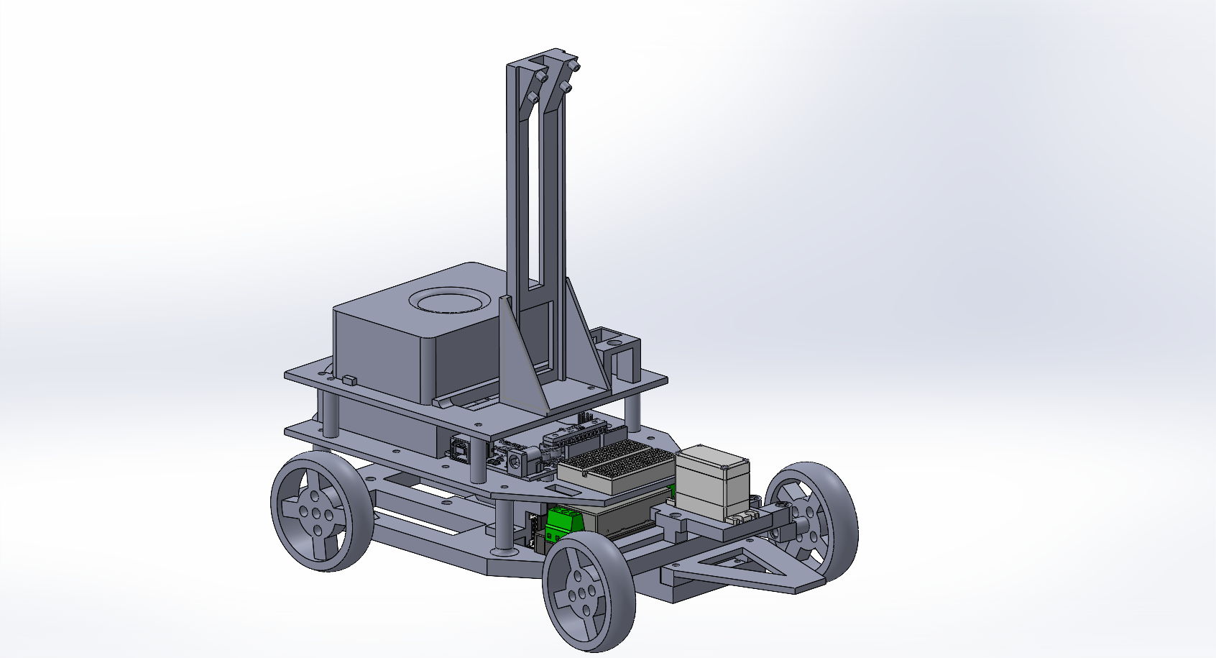
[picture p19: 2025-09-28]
v-photos/3D_Printed_PNG/DrivingRobot2.PNG

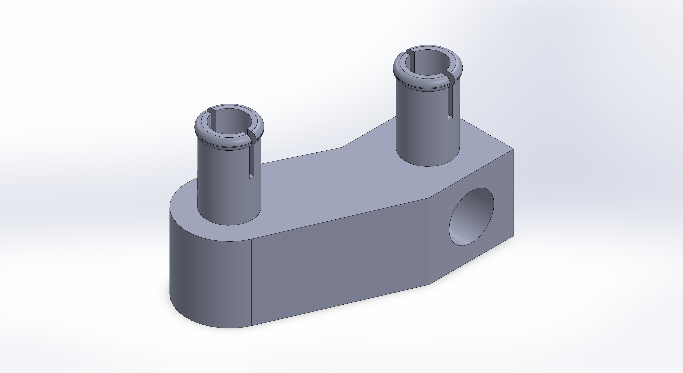
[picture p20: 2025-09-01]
v-photos/3D_Printed_PNG/DirectionTabsRH.PNG

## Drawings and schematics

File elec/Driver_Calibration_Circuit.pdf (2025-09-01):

# ÏÏÏÏ

# ÏËÏÏÏ

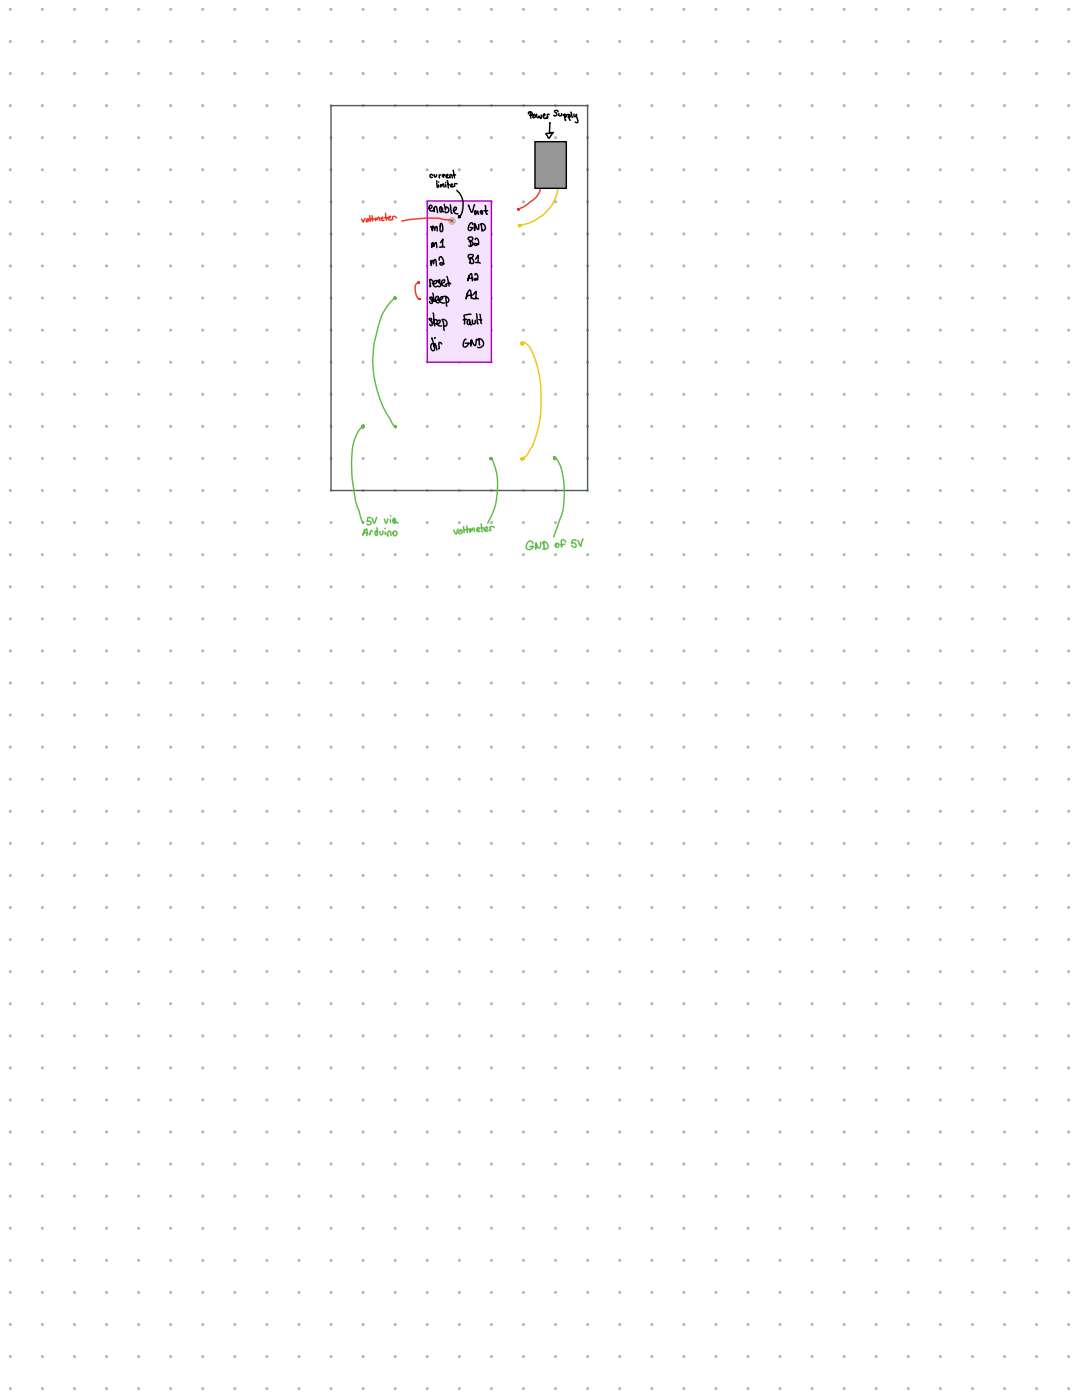
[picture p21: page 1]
rouergsuppig; j 15jui; voltmeter; ans su

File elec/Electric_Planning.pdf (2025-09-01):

S

## Raspberry Pi 5

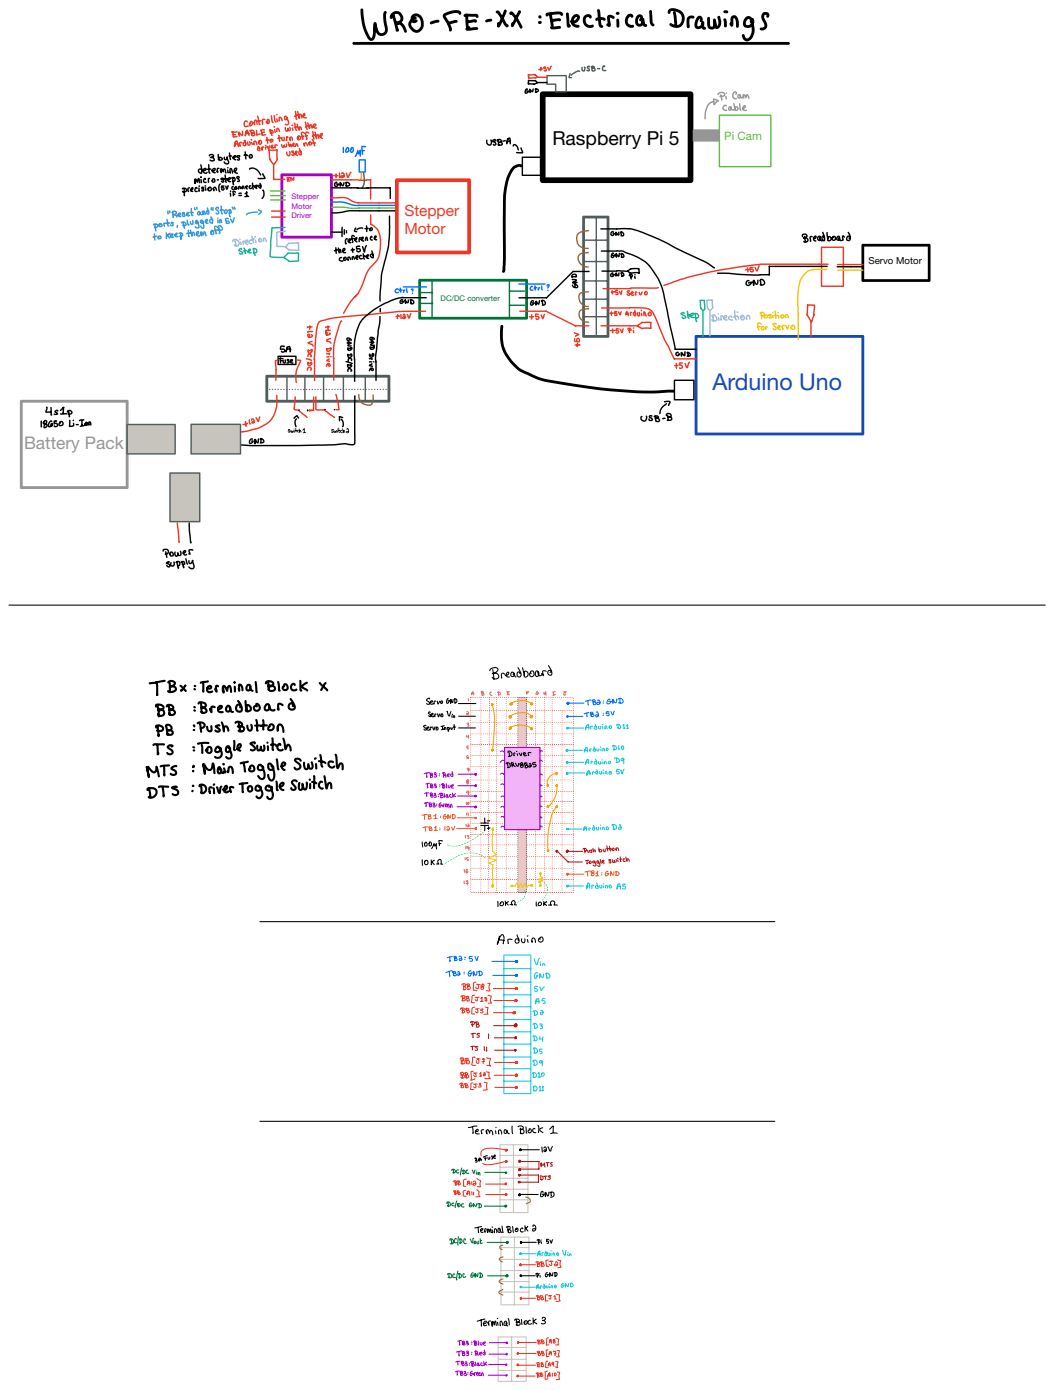
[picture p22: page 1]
usine; usB.mn; ËïÏÏ; À'Eton; IHEEIII; Arduino Uno; Stepper Motor; Servo Motor; Pi Cam; Stepper Motor Driver; Battery Pack

DC/DC converter

Breadboard ïÏiËïÏiÏÏÏÏ'ÏÉÏÏÉÏÏÏÉÏÏÏÏÉIIIIIIIIIIIIIÉFÉÏIIII

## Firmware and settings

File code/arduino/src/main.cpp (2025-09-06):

/// @file main.cpp
/// @brief Main file for controlling the stepper motor and servo
/// @author Michael Bruneau
/// @date 24-07-2025
/// @version 2.0 : Added voltage measurement and improved command handling

#include <Arduino.h>
#include <FlexyStepper.h>
#include <Servo.h>
#include "utils/voltage_utils.h"
#include "classes/serial_reciever.h"

const int DIR_PIN = 10;       // Pin for stepper motor direction
const int STEP_PIN = 9;      // Pin for stepper motor control
const int ENABLE_PIN = 2;   // Pin for enabling/disabling the stepper motor
const int ANGLE_PIN = 11;    // Pin for servo control
const int START_BTN_PIN = 3; // Pin for start button
const int CHALLENGE_1_PIN = 4; // Pin for challenge 1 button
const int CHALLENGE_2_PIN = 5; // Pin for challenge 2 button

const int ACCELERATION = 2000; // Acceleration for the stepper motor

const float WHEEL_DIAMETER = 55.6; // Wheel diameter in mm
const int STEPS_PER_REVOLUTION = 200; // Steps per revolution for the stepper motor
const float MICROSTEPS = 0.25; // Microstepping factor for the stepper motor
const float GEAR_RATIO = 10 / 14; // Gear ratio for the stepper motor
//const float STEPS_PER_MM = STEPS_PER_REVOLUTION / MICROSTEPS

// Voltage divider for battery voltage measurement
const int R1 = 20000;       // Resistor R1 in ohms
const int R2 = 10000;       // Resistor R2 in ohms

int angle = 88;             // initial angle for the servo
int speed = 0;              // initial speed for the stepper
long int targetPosition = -10000000;    // target position for the stepper

bool buttonPressed = false; // Flag to indicate if the button is pressed already
unsigned long lastDebounceTime = 0; // the last time the output pin was toggled
const unsigned long debounceDelay = 50; // the debounce time for the start button

String inputString = "";    // a string to hold incoming data

Servo servo;                // Create a Servo object
FlexyStepper stepper;       // Create a FlexyStepper object
SerialReceiver serialReceiver(servo, stepper, angle, speed, targetPosition);

void processStartButton();
int getSelectedChallenge();

void setup() {
    Serial.begin(115200);
    servo.attach(ANGLE_PIN);

    stepper.connectToPins(STEP_PIN, DIR_PIN);
    stepper.setCurrentPositionInSteps(0);
    stepper.setTargetPositionInSteps(0);
    stepper.setAccelerationInStepsPerSecondPerSecond(ACCELERATION);
    stepper.setSpeedInStepsPerSecond(speed);
    serialReceiver.waitingForTarget = false;
    pinMode(ENABLE_PIN, OUTPUT);
    digitalWrite(ENABLE_PIN, LOW);

    pinMode(START_BTN_PIN, INPUT_PULLUP);
    pinMode(CHALLENGE_1_PIN, INPUT_PULLUP);
    pinMode(CHALLENGE_2_PIN, INPUT_PULLUP);
}

void loop() {
    processStartButton();
    if (speed == 0 && abs(stepper.getCurrentVelocityInStepsPerSecond()) < 100) {
        digitalWrite(ENABLE_PIN, HIGH); // Disable stepper when speed is 0
    } else {
        digitalWrite(ENABLE_PIN, LOW); // Enable stepper when speed is not 0
        stepper.processMovement();
    }
    serialReceiver.processSerial();
    if (stepper.motionComplete() && serialReceiver.waitingForTarget) {
        Serial.println("F");
        serialReceiver.waitingForTarget = false; // Reset waiting for target flag
        speed = 0; // Stop the stepper motor
    }
}


int getSelectedChallenge() {
    if (digitalRead(CHALLENGE_1_PIN) == LOW) {
        return 1;
    } else if (digitalRead(CHALLENGE_2_PIN) == LOW) {
        return 2;
    } else {
        return 0; // No challenge selected
    }
}

void processStartButton() {
    int challenge = getSelectedChallenge();
    
    bool currentButtonState = (digitalRead(START_BTN_PIN) == LOW);
    
    if (currentButtonState && !buttonPressed && 
        (millis() - lastDebounceTime) > debounceDelay) {
        buttonPressed = true;
        lastDebounceTime = millis();
            Serial.println(String(challenge));
    } else if (!currentButtonState) {
        buttonPressed = false;
    }
}

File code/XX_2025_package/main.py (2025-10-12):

import serial
import cv2
import time
import numpy as np
from classes.camera_manager import CameraManager
from utils.image_transform_utils import ImageTransformUtils
from classes.image_algoriths import ImageAlgorithms
from classes.context_manager import ContextManager
from classes.lap_tracker import LapTracker
from utils.enums import Direction
from utils.enums import StartPosition
from utils.image_drawing_utils import ImageDrawingUtils
from classes.arduino_comms import ArduinoComms

MOVE_TO_FRONT_ZONE = 2700
stop_run = False

# 0.1559 mm per 1 step
# 1 mm per 6.412 steps

if __name__ == "__main__":
    camera_manager = CameraManager()
    while True: # main loop to allow multiple runs without restarting
        ## 0 ##
        # Initialize program, camera, etc
        context_manager = ContextManager()
        lap_tracker = LapTracker(context_manager)
        image_algorithms = ImageAlgorithms(context_manager, camera_manager)
        arduino = ArduinoComms()
        camera_manager.start_camera()
        arduino.send('!', 10000000)

        # Run the image analysis once to initialize variables
        camera_manager.capture_image()
        camera_manager.transform_image()

        ## 1 ##
        # Wait for start button to be pressed
        while True:
            msg = arduino.read()
            if msg:
                if msg == '1':
                    context_manager.set_challenge(1)
                    print("Challenge 1 selected")
                    break
                    
                elif msg == '2':
                    context_manager.set_challenge(2)
                    print("Challenge 2 selected")
                    break

                elif msg == '0':
                    print("Leave program")
                    stop_run = True
                    break
                time.sleep(0.005)

        if stop_run:
            break
        #time.sleep(1)
        camera_manager.capture_image()
        camera_manager.transform_image()

        ################################################################
        ############################ Défi 1 ############################
        ################################################################
        
        if (ContextManager.CHALLENGE == 1):
            check_corner_flag = False
            start_time = 0
            speed = 5500

            # 1. Find direction with blue and orange lines
            image_algorithms.get_direction_from_lines()
            print("Direction : ", context_manager.get_direction())

            # 2. Find starting area
            start_position = image_algorithms.get_starting_position()
            print("Start position: ", start_position)
            context_manager.set_start_position(start_position)

            # 3. Complete 3 laps
            while True:
                camera_manager.capture_image()
                camera_manager.transform_image()
                lap_tracker.process_image(camera_manager.cnt_blueline, camera_manager.cnt_orangeline)
                angle, is_corner = image_algorithms.calculate_servo_angle_from_walls()
                arduino.send('m', angle, speed)
                ImageDrawingUtils.add_text_to_image(camera_manager.display_image, f"Lap: {context_manager.get_lap_count()}", (10, 30), (0, 0, 255))
                camera_manager.add_frame_to_video()
                cv2.imshow("Display", camera_manager.display_image)

                # 4. Check last corner and stop the robot in the correct zone
                if (context_manager.is_last_quarter() or context_manager.has_completed_laps()):
                    speed = 4000
                    if start_time == 0:
                        start_time = time.time()
                    if (time.time() - start_time >= 1) and is_corner and not check_corner_flag:
                        print("Corner !")
                        check_corner_flag = True
                        final_corner_position = image_algorithms.check_last_corner_position()
                        print("Here's the final corner ! The outside wall is : ", final_corner_position)
                        # Add extra_move based on start position
                        if context_manager.get_start_position() == StartPosition.FRONT:
                            extra_move = MOVE_TO_FRONT_ZONE
                        else:
                            extra_move = 0
                        # Adjust move based on final corner position
                        if final_corner_position == 'C':
                            arduino.send('!', 6900)
                            speed = 1500
                        else:
                            arduino.send('!', 4400)
                            speed = 1500
                if context_manager.has_completed_laps() and arduino.read() == 'F':
                    break
                # Let OpenCV update the window
                key = cv2.waitKey(1)  
                # Press escape key to quit (when testing)
                if key == 27:
                    if (speed != 0):
                        speed = 0
                    else:
                        break
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

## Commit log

2025-07-17 arduino(new): inital code to trigger led based on data sent by Pi
2025-07-17 pi(new) : code to send signal to arduino, to flash the built-in LED
2025-07-24 arduino(edit): main code controls the robot's motors via serial
2025-07-24 arduino(edit): add voltage check to the main.cpp, and reorganize the code in various functions
2025-07-24 arduino(refactor): changed consts for upper snake case
2025-07-31 arduino(refactor): refactored main in separate classes
2025-07-31 arduino(fix): changed serial reading to be faster
    [main.cpp, serial_reciever.cpp]
2025-07-31 pi(edit):code to do laps around the circuits, improvements on the wall detection
2025-08-01 arduino(adjust): adjusted acceleration
2025-08-03 pi(edit): this code works for laps around the track, counterclockwise, with great reliability, although it can only start from 3 of the 6 starting zones, and doesn't stop by itself
    [main.py]
2025-08-07 pi(rebuild): this version works since the previous version had a smaller bug
    [image_algoriths.py, main.py, map_plotter.py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]
2025-08-08 pi(edit): add useful attributes to camera_manager such as masks for all colors, so the camera now detects the obstacles only, and very well, next step is to adjust the algo to know which color the ob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
2025-08-09 pi(new): version 1 of navigating around objects, it works at speed = 3000, but has some issues where it can bump the inner wall and in some cases the outer wall too
    [camera_manager.py, image_algoriths.py, image_utils.py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]
2025-08-12 pi(edit): optimizing the obstacle challenge, we figured out which combinations were harder, still trying to add the proper corrections to the code. We also started the parking logic, but no progress 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
    [camera_manager.py, image_algoriths.py, image_utils.py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]
2025-08-12 pi(new): added context manager class that will keep track of direction, lap count, etc
2025-08-12 fix(pi): forgot delay in other function
    [lap_tracker.py]
2025-08-13 arduino(new): updated arduino code to receive a distance in steps and then changing the target_position to the one received. it stops afterwards
2025-08-14 fix(pi): fixed line coords depending on turn direction
    [lap_tracker.py]
2025-08-14 fix(pi): lap tracker missing color enum
    [context_manager.py, lap_tracker.py]
2025-08-14 pi(edit): fixing the get_direction from parking
    [camera_manager.py, context_manager.py, image_algoriths.py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]
2025-08-14 arduino(new): change the serial reading so that it doesn't block everything else and stop the stepper motor's feeding
    [main.cpp, serial_reciever.cpp, serial_reciever.h]
2025-08-15 pi(new): missing file in last commit
    [image_algoriths.py]
2025-08-15 pi(new): detect direction from parking works, stops after 3 laps in challenge 2 works, code for reading F from arduino in progress
2025-08-15 pi(new): pi read arduino message correctly, can now wait for arduino to send the message before continuing
    [context_manager.py, main.py]
2025-08-15 global(new): added XX_Parts_Lists.xlsx, and added consts to Arduino code for future mm implementation
    [XX_Parts_Lists.xlsx]
2025-08-17 pi(new): fixed 2 out of 3 hard combinations : starting areas of challenge 1, and exterior avoidance in challenge 2, next fix we're trying is the inner wall clipping
    [camera_manager.py, image_algoriths.py, image_transform_utils.py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]
2025-08-17 pi(new): fixing the inner wall clipping, potentially some probabilities of failing still, but great improvement. Next step is commenting the code and making it clearer since it is currently quite a m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
    [context_manager.py, image_algoriths.py, image_drawing_utils.py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]
2025-08-18 pi(new): make code clearer, starting with image_algorithms, cleaning the find_target_servo_angle_from_img( ) function, and everything it calls, and every fct before too. Also, new version of the thre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
    [image_algoriths.py]
2025-08-20 pi(edit): refactor setup video output in camera manager
2025-08-20 pi(fix): fix more video with binary img
    [camera_manager.py]
2025-08-20 pi(fix): lap count display on image
    [lap_tracker.py]
2025-08-21 Arduino(new): now able to change target separately, just need to enter : 1500!
2025-08-22 Arduino(edit): fixed bug with new implementation, now everything works as we want. Next step (if there's one) would be to implement mm instead of steps, but we might do it only in the Pi
    [main.cpp, serial_reciever.cpp]
2025-08-24 arduino(new): start button listening
2025-08-24 fix(arduino): remove forgotten delay
    [main.cpp]
2025-08-24 pi(new): button detection, main loops
2025-08-24 pi(edit): fix bug where it would capture the image before pressing the button
    [image_algoriths.py, main.py]
2025-08-29 choice of Spike Prime wheels in README (test format too)
2025-08-30 Revise README for clarity on mechanical design choices
    Updated the README to clarify wheel choice, steering systems, and structural prototypes. Improved descriptions for better understanding of design decisions and component layout.
2025-08-30 Revise electrical design documentation for clarity
    Updated the electrical design documentation to enhance clarity and precision regarding motor choices, components, and architecture.
2025-08-31 arduino(new): CHANGE DIGITAL PINS 2 AND 10 FOR BETTER CABLE MANAGEMENT
2025-09-01 global(new): added all CAD files
    [BasePlaqueV4.STEP, BasePlaqueV4.STL, ButtonHolder.STEP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]
2025-09-01 global(edit): change name of CAD folder for linking images
    [BasePlaqueV4.STEP, BasePlaqueV4.STL, ButtonHolder.STEP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]
2025-09-01 global(edit): again I guess
    [BasePlaqueV4.STEP, BasePlaqueV4.STL, ButtonHolder.STEP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]
2025-09-01 Add Raspberry Pi 5 setup guide for Python development
2025-09-01 Add Raspberry Pi environment setup section to README
2025-09-01 Enhance README with images and assembly details
    Added images and building instructions for the robot.
2025-09-01 Rename Driver Calibration Circuit.pdf to Driver_Calibration_Circuit.pdf
2025-09-01 Revise 3D printing and assembly instructions
    Updated instructions for 3D printing parts and robot assembly, including adjustments for the DRV8825 driver.
2025-09-02 Add motor control documentation for Team Double-X
    This document details the motor control system for Team Double-X's robot, including hardware architecture, software implementation, control flow, and temperature analysis.
2025-09-02 Revise motor control documentation for clarity
    Updated explanations regarding stepper motor control and driver overheating, including changes to thermal image descriptions and references.
2025-09-06 Enhance README with Ackermann steering and images
2025-09-06 Enhance README with CAD images and views
2025-09-06 Update motor_control.md with thermal images
2025-09-07 Enhance README with motor torque calculations
2025-09-07 Specify Prusa Core 1 for 3D printing parts
    Added specific printer model used for 3D printing.
2025-09-13 pi(new): fix detection of last obstacle, add adjustment in consequence
    [context_manager.py, image_algoriths.py, main.py]
2025-09-28 pi(new) : added arduino_comms class and update main
    [FrontWingV2.STEP, FrontWingV2.STL]
2025-09-28 pi(new): new comms work, fixed import paths
    [HSV_ajuster.py, arduino_comms.py, camera_manager.py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]
2025-09-28 pi(new): change kp when inner wall crash detection
    [image_algoriths.py]
2025-10-11 pi(new): main.py : increasing speed while following obstacles, accelerating in parking sequence, run the image analysis once to initialize variables (to save 1 sec), remove time.sleep(1) at beginning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
    [image_algoriths.py, image_color_utils.py, main.py]
2025-10-12 pi(edit) : fix the new run.py, fix the first quarter lap slow reaction, try to fix the inner_wall / outer_wall conflict, but still work to do
    [image_algoriths.py, main.py, run.py]
2025-10-13 pi(refactor): moved video to thread, added timer and state info to display
2025-10-23 pi(new): make proper changes to make camera_manager's main work. Also, we added a function to determine whether the robot is correctly inside the parking area or not, useful for later
    [camera_manager.py, image_algoriths.py, run.py]
2025-10-23 pi(fix): added a proper lock mecanism for video thread
    [camera_manager.py, info_overlay_processor.py, run.py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]
2025-10-23 pi(fix): debuging video thread
    [run.py, video_thread.py]
2025-10-23 pi(video): new thread signals to capture images
2025-10-23 pi(fix): thread crashing when queue empty
    [run.py, video_thread.py]
2025-10-23 pi(fix): added proper video release
    [camera_manager.py, run.py, video_thread.py]
2025-10-24 pi(chore): remove old print statements
2025-10-24 pi(edit): fix the bug where it takes a picture only inside the parking and uses it for its first adjustment in laps.
    [image_algoriths.py, run.py, video_thread.py]
2025-10-26 pi(new): set the fixed value of FPS at 24 instead of 15 since we take more images, remove the line where display image was set to cropped image (this was removing the pink contours of obstacles), add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
    [HSV_ajuster.py, camera_manager.py, context_manager.py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]
2025-11-07 git(new): images folder and more
    [CanadianFlag.STL, ServoCover.SLDPRT, ServoCover.STL]
2025-11-07 Switch sections
